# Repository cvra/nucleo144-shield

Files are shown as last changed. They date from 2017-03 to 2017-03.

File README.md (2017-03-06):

# CVRA Nucleo144 shield

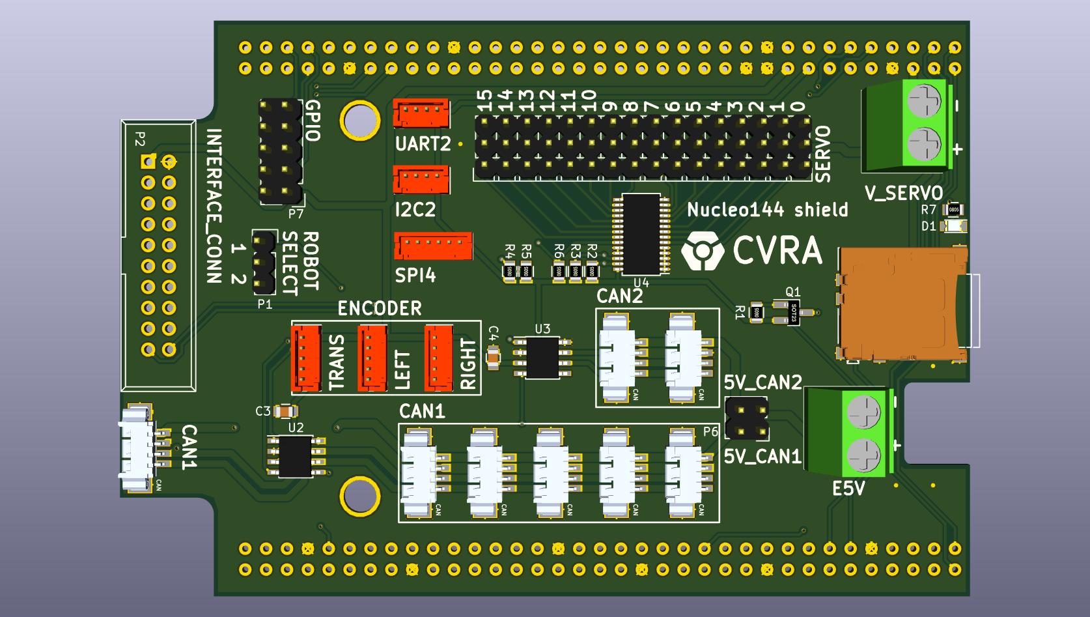
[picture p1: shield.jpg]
assembled PCB


## Requirements list
* Alim en entrée
 - 5V, bus + nucleo + shield (borne à visser)
 - 6V, servo (borne à visser)
* debug connector
* 2x CAN interface with CAN transceiver:
  - 6x Connector for one CAN interface (mounted as needed)
  - 3x Connector for other CAN interface (mounted as needed)
* Interface panel connector (20 pin)
  - 5V, GND (2 pin)
  - 2x CAN for debug (1 for each interface) (4 pin)
  - RGB LED (3 GPIO to control) (3 pin)
  - I/O (11 pin)
* 15x RC-Servo output: connecteur 3pin 2.54mm standard (+,-,signal). use PWM if available and GPIO for the rest (software PWM)
* 2x Encoder connector (5-pin Molex CHA, CHB, CHN, 5V, GND)
(3x Encoder connector if I/O available on MCU)
* Additional connectors (if I/O available on MCU)
  - 1x I2C Molex
  - 1x UART Molex
  - 1x SPI Molex
  - 4x GPIO (with 4x GND) on 2.54mm standard pin holes (no connector)
  - 1x 5V power to power board and distribute over CAN
* SDCard/SPI-flash for logging
* Mechanical dimension
  - Width and length, max same as Nucleo-144 board (70mmx108mm)
  - Maximum mechanical available space including output cable for Nucleo board and shield ( height = 36mm, lenght = 136.5mm)

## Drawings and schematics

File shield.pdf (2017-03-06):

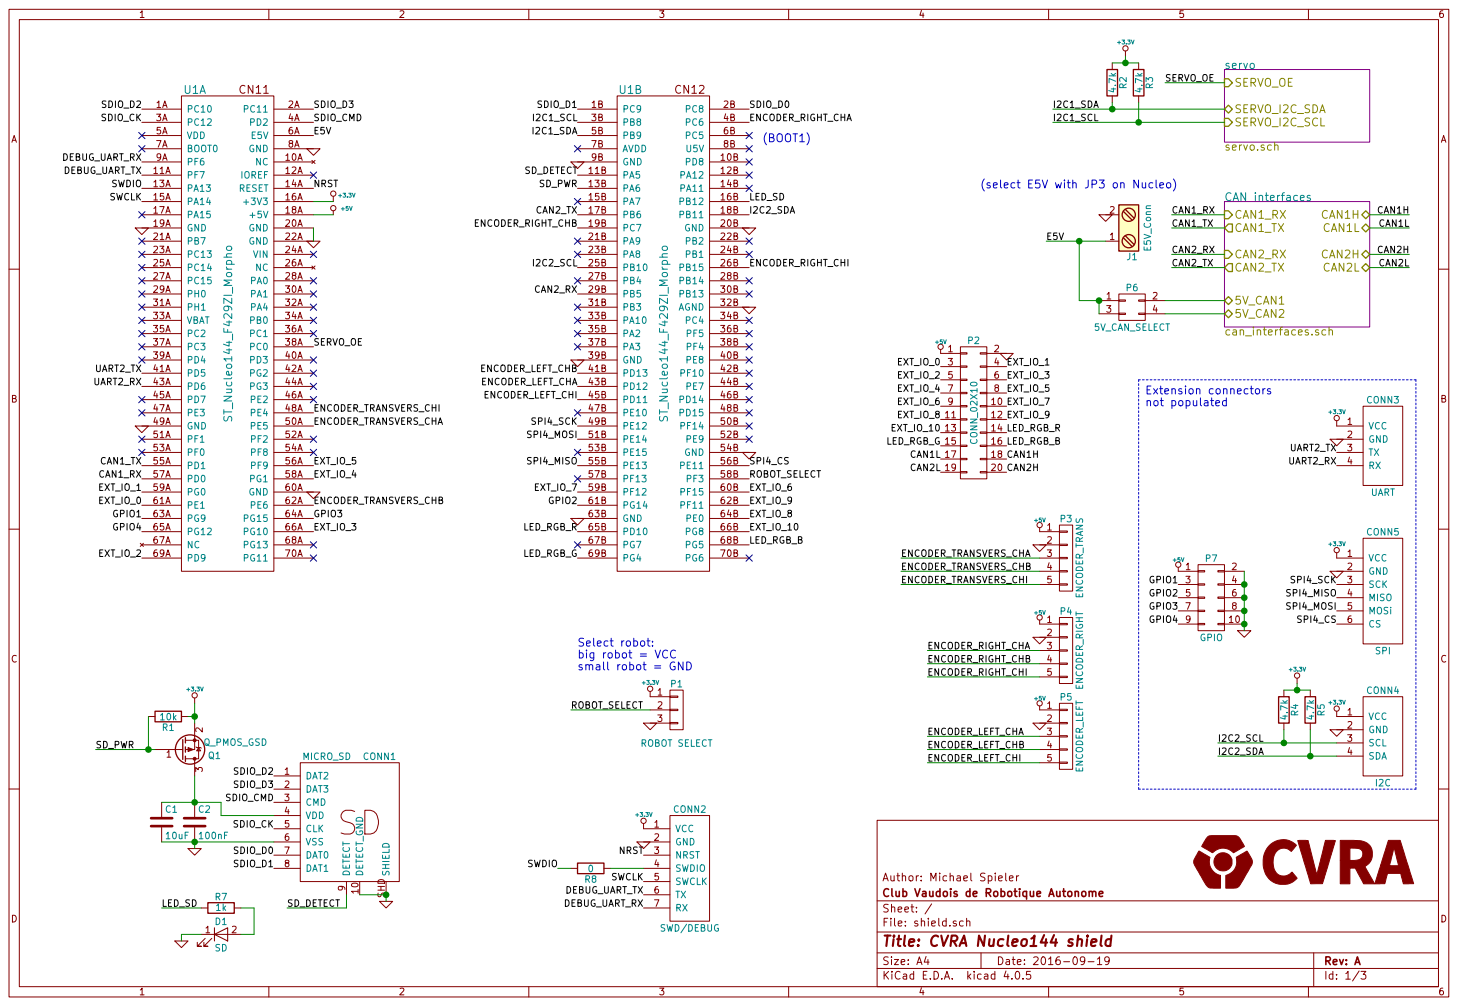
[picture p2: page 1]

Author: Michael Spieler
File: shield.sch Sheet: / Club Vaudois de Robotique Autonome

Id: 1/3 Title: CVRA Nucleo144 shield

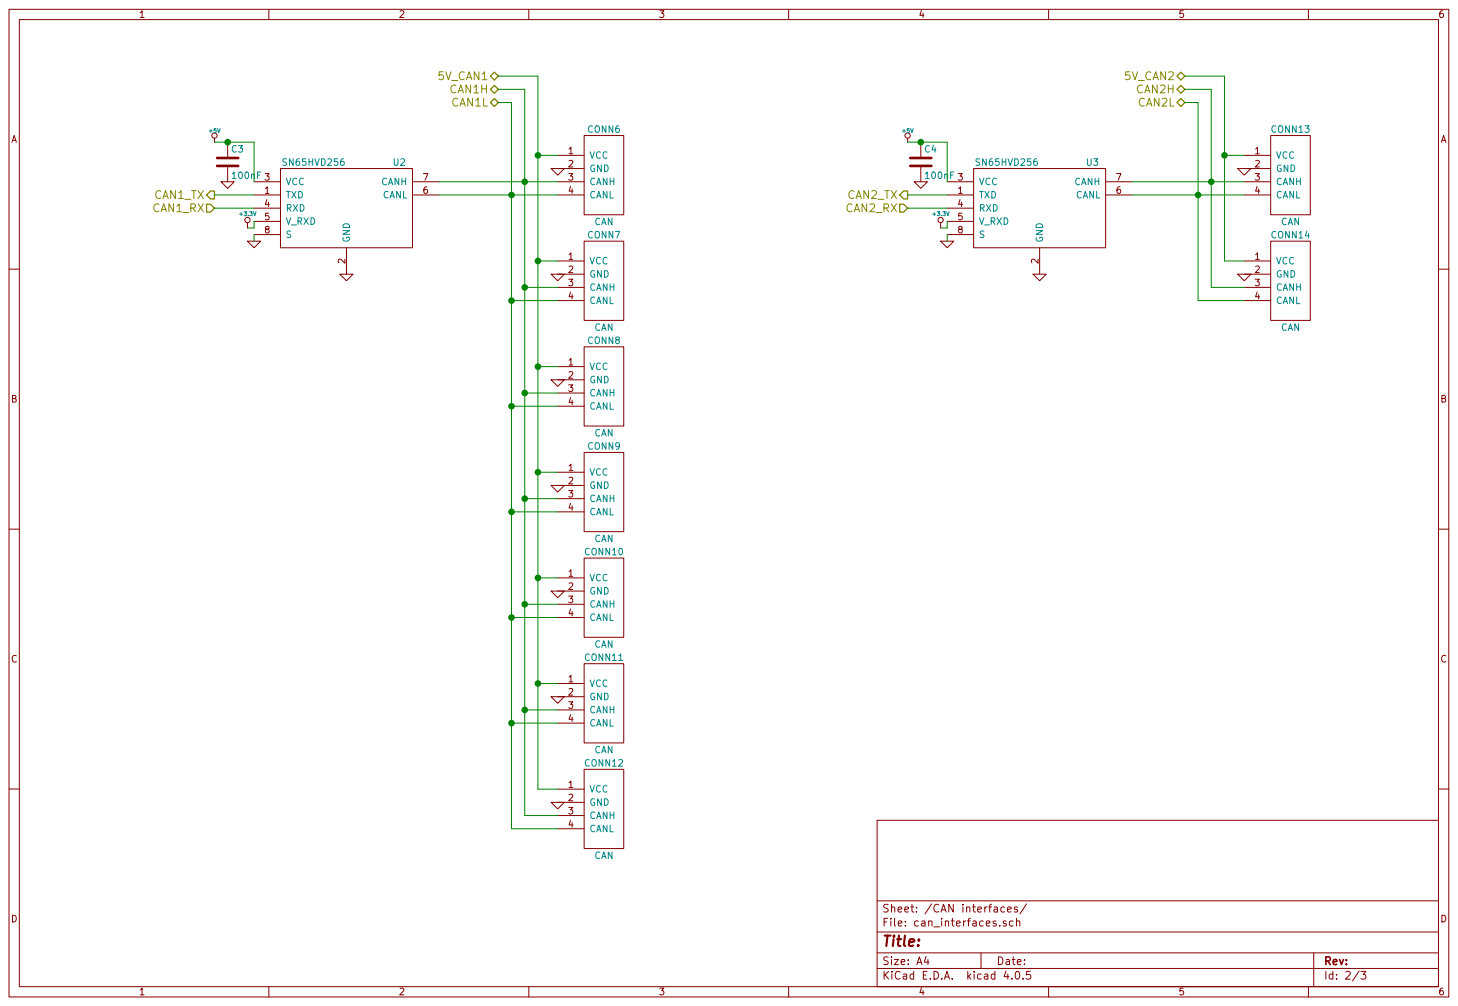
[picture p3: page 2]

File: can_interfaces.sch Sheet: /CAN interfaces/

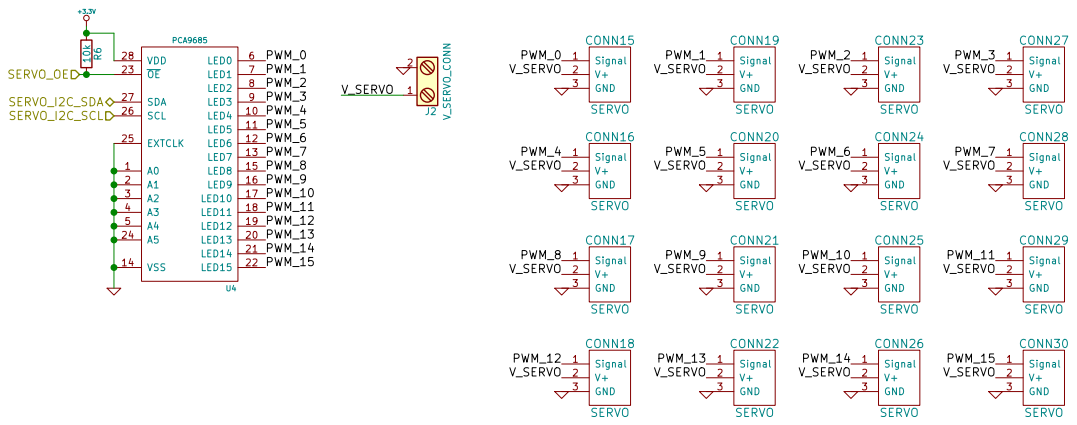
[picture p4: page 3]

Id: 3/3 Title: File: servo.sch Sheet: /servo/

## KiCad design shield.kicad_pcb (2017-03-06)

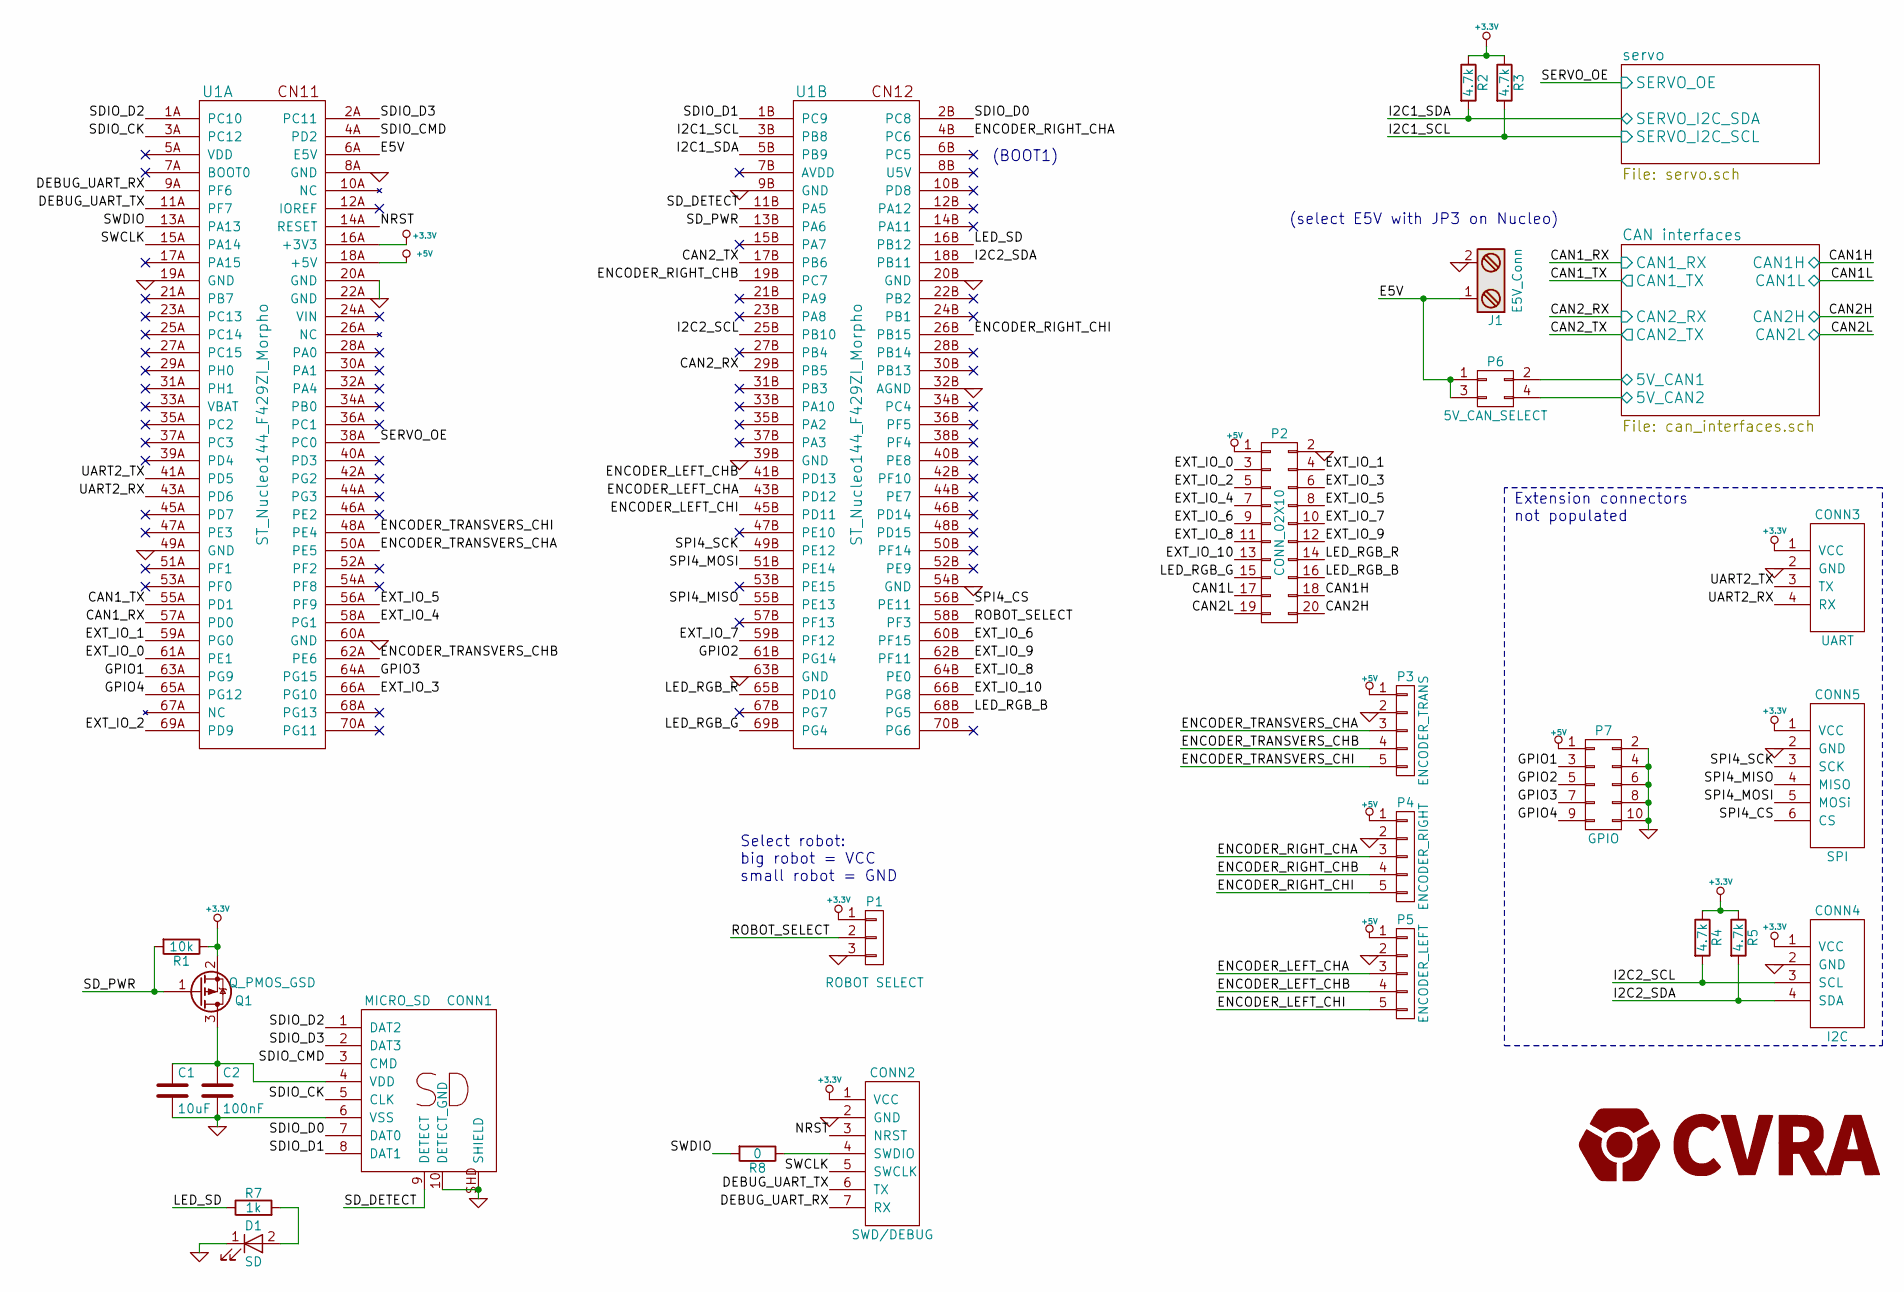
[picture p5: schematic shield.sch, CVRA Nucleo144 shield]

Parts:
C1: 10uF; C_0805
C2: 100nF; C_0805
CONN1: MICRO_SD; _Molex-microSD-502570-0893
CONN2: SWD/DEBUG; Molex_PicoBlade_53261-0771_07x1.25mm_Angled
CONN3: UART; Molex-PicoBlade-4
CONN4: I2C; Molex-PicoBlade-4
CONN5: SPI; Molex-PicoBlade-6
D1: SD; LED_0805
J1: E5V_Conn; TerminalBlock_Pheonix_MKDS1.5-2pol
P1: ROBOT SELECT; Pin_Header_Straight_1x03
P2: CONN_02X10; IDC_Header_Straight_20pins
P3: ENCODER_TRANS; Molex-PicoBlade-5
P4: ENCODER_RIGHT; Molex-PicoBlade-5
P5: ENCODER_LEFT; Molex-PicoBlade-5
P6: 5V_CAN_SELECT; Pin_Header_Straight_2x02
P7: GPIO; Pin_Header_Straight_2x05
Q1: Q_PMOS_GSD; SOT-23_Handsoldering
R1: 10k; R_0805
R2, R3, R4, R5: 4.7k; R_0805
R7: 1k; R_0805
R8: 0; R_0805
U1: ST_Nucleo144_F429ZI_Morpho

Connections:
+3.3V: CONN2.1 (VCC), CONN3.1 (VCC), CONN4.1 (VCC), CONN5.1 (VCC), P1.1, Q1.2 (S), R1.1, R2.1, R3.1, R4.1, R5.1, U1.16A (+3V3); also elsewhere on the board
+5V: P2.1, P3.1, P4.1, P5.1, P7.1, U1.18A (+5V); also elsewhere on the board
/CAN1H: P2.18; also elsewhere on the board
/CAN1L: P2.17; also elsewhere on the board
/CAN1_RX: U1.57A (PD0); also elsewhere on the board
/CAN1_TX: U1.55A (PD1); also elsewhere on the board
/CAN2H: P2.20; also elsewhere on the board
/CAN2L: P2.19; also elsewhere on the board
/CAN2_RX: U1.29B (PB5); also elsewhere on the board
/CAN2_TX: U1.17B (PB6); also elsewhere on the board
/CAN interfaces/5V_CAN1: P6.2; also elsewhere on the board
/CAN interfaces/5V_CAN2: P6.4; also elsewhere on the board
/DEBUG_UART_RX: CONN2.7 (RX), U1.9A (PF6)
/DEBUG_UART_TX: CONN2.6 (TX), U1.11A (PF7)
/E5V: J1.1, P6.1, P6.3, U1.6A (E5V)
/ENCODER_LEFT_CHA: P5.3, U1.43B (PD12)
/ENCODER_LEFT_CHB: P5.4, U1.41B (PD13)
/ENCODER_LEFT_CHI: P5.5, U1.45B (PD11)
/ENCODER_RIGHT_CHA: P4.3, U1.4B (PC6)
/ENCODER_RIGHT_CHB: P4.4, U1.19B (PC7)
/ENCODER_RIGHT_CHI: P4.5, U1.26B (PB15)
/ENCODER_TRANSVERS_CHA: P3.3, U1.50A (PE5)
/ENCODER_TRANSVERS_CHB: P3.4, U1.62A (PE6)
/ENCODER_TRANSVERS_CHI: P3.5, U1.48A (PE4)
/EXT_IO_0: P2.3, U1.61A (PE1)
/EXT_IO_1: P2.4, U1.59A (PG0)
/EXT_IO_2: P2.5, U1.69A (PD9)
/EXT_IO_3: P2.6, U1.66A (PG10)
/EXT_IO_4: P2.7, U1.58A (PG1)
/EXT_IO_5: P2.8, U1.56A (PF9)
/EXT_IO_6: P2.9, U1.60B (PF15)
/EXT_IO_7: P2.10, U1.59B (PF12)
/EXT_IO_8: P2.11, U1.64B (PE0)
/EXT_IO_9: P2.12, U1.62B (PF11)
/EXT_IO_10: P2.13, U1.66B (PG8)
/GPIO1: P7.3, U1.63A (PG9)
/GPIO2: P7.5, U1.61B (PG14)
/GPIO3: P7.7, U1.64A (PG15)
/GPIO4: P7.9, U1.65A (PG12)
/I2C1_SCL: R3.2, U1.3B (PB8); also elsewhere on the board
/I2C1_SDA: R2.2, U1.5B (PB9); also elsewhere on the board
/I2C2_SCL: CONN4.3 (SCL), R4.2, U1.25B (PB10)
/I2C2_SDA: CONN4.4 (SDA), R5.2, U1.18B (PB11)
/LED_RGB_B: P2.16, U1.68B (PG5)
/LED_RGB_G: P2.15, U1.69B (PG4)
/LED_RGB_R: P2.14, U1.65B (PD10)
/LED_SD: R7.1, U1.16B (PB12)
/NRST: CONN2.3 (NRST), U1.14A (RESET)
/ROBOT_SELECT: P1.2, U1.58B (PF3)
/SDIO_CK: CONN1.5 (CLK), U1.3A (PC12)
/SDIO_CMD: CONN1.3 (CMD), U1.4A (PD2)
/SDIO_D0: CONN1.7 (DAT0), U1.2B (PC8)
/SDIO_D1: CONN1.8 (DAT1), U1.1B (PC9)
/SDIO_D2: CONN1.1 (DAT2), U1.1A (PC10)
/SDIO_D3: CONN1.2 (DAT3), U1.2A (PC11)
/SD_DETECT: CONN1.9 (DETECT), U1.11B (PA5)
/SD_PWR: Q1.1 (G), R1.2, U1.13B (PA6)
/SERVO_OE: U1.38A (PC0); also elsewhere on the board
/SPI4_CS: CONN5.6 (CS), U1.56B (PE11)
/SPI4_MISO: CONN5.4 (MISO), U1.55B (PE13)
/SPI4_MOSI: CONN5.5 (MOSi), U1.51B (PE14)
/SPI4_SCK: CONN5.3 (SCK), U1.49B (PE12)
/SWCLK: CONN2.5 (SWCLK), U1.15A (PA14)
/SWDIO: R8.2, U1.13A (PA13)
/UART2_RX: CONN3.4 (RX), U1.43A (PD6)
/UART2_TX: CONN3.3 (TX), U1.41A (PD5)
GND: C1.2, C2.2, CONN1.6 (VSS), CONN1.10 (DETECT_GND), CONN1.SHD (SHIELD), CONN2.2 (GND), CONN3.2 (GND), CONN4.2 (GND), CONN5.2 (GND), D1.1 (K), J1.2, P1.3, P2.2, P3.2, P4.2, P5.2, P7.2, P7.4, P7.6, P7.8, P7.10, U1.8A (GND), U1.9B (GND), U1.19A (GND), U1.20A (GND), U1.20B (GND), U1.22A (GND), U1.32B (AGND), U1.39B (GND), U1.49A (GND), U1.54B (GND), U1.60A (GND), U1.63B (GND); also elsewhere on the board
unnamed: C1.1, C2.1, CONN1.4 (VDD), Q1.3 (D)
unnamed: CONN2.4 (SWDIO), R8.1
unnamed: D1.2 (A), R7.2

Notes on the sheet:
Select robot: big robot = VCC small robot = GND
(BOOT1)
(select E5V with JP3 on Nucleo)
Extension connectors not populated

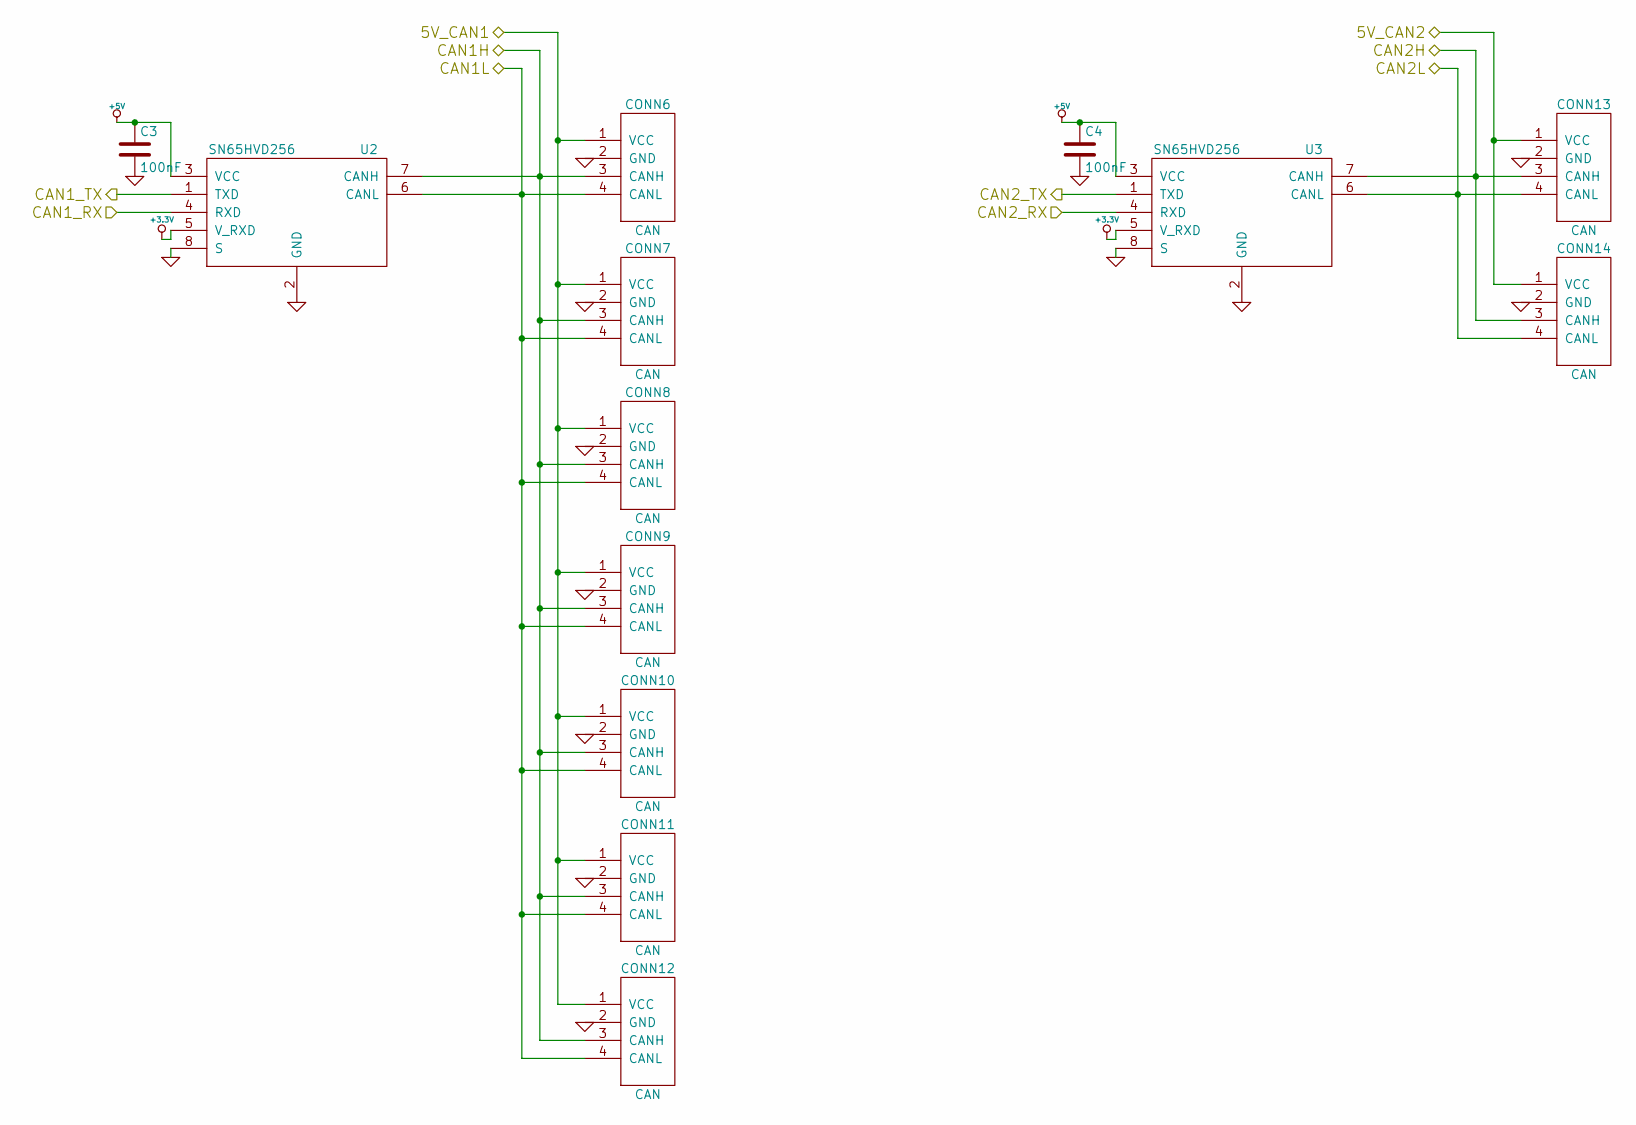
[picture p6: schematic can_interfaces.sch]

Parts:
C3, C4: 100nF; C_0805
CONN6, CONN7, CONN8, CONN9, CONN10, CONN11, CONN12, CONN13, CONN14: CAN; _Molex-PicoBlade-SMD-4
U2, U3: SN65HVD256; SOIC-8_3.9x4.9mm_Pitch1.27mm

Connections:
+3.3V: U2.5 (V_RXD), U3.5 (V_RXD); also elsewhere on the board
+5V: C3.1, C4.1, U2.3 (VCC), U3.3 (VCC); also elsewhere on the board
/CAN1H: CONN6.3 (CANH), CONN7.3 (CANH), CONN8.3 (CANH), CONN9.3 (CANH), CONN10.3 (CANH), CONN11.3 (CANH), CONN12.3 (CANH), U2.7 (CANH); also elsewhere on the board
/CAN1L: CONN6.4 (CANL), CONN7.4 (CANL), CONN8.4 (CANL), CONN9.4 (CANL), CONN10.4 (CANL), CONN11.4 (CANL), CONN12.4 (CANL), U2.6 (CANL); also elsewhere on the board
/CAN1_RX: U2.4 (RXD); also elsewhere on the board
/CAN1_TX: U2.1 (TXD); also elsewhere on the board
/CAN2H: CONN13.3 (CANH), CONN14.3 (CANH), U3.7 (CANH); also elsewhere on the board
/CAN2L: CONN13.4 (CANL), CONN14.4 (CANL), U3.6 (CANL); also elsewhere on the board
/CAN2_RX: U3.4 (RXD); also elsewhere on the board
/CAN2_TX: U3.1 (TXD); also elsewhere on the board
/CAN interfaces/5V_CAN1: CONN6.1 (VCC), CONN7.1 (VCC), CONN8.1 (VCC), CONN9.1 (VCC), CONN10.1 (VCC), CONN11.1 (VCC), CONN12.1 (VCC); also elsewhere on the board
/CAN interfaces/5V_CAN2: CONN13.1 (VCC), CONN14.1 (VCC); also elsewhere on the board
GND: C3.2, C4.2, CONN6.2 (GND), CONN6.MECH (GND), CONN7.2 (GND), CONN7.MECH (GND), CONN8.2 (GND), CONN8.MECH (GND), CONN9.2 (GND), CONN9.MECH (GND), CONN10.2 (GND), CONN10.MECH (GND), CONN11.2 (GND), CONN11.MECH (GND), CONN12.2 (GND), CONN12.MECH (GND), CONN13.2 (GND), CONN13.MECH (GND), CONN14.2 (GND), CONN14.MECH (GND), U2.2 (GND), U2.8 (S), U3.2 (GND), U3.8 (S); also elsewhere on the board

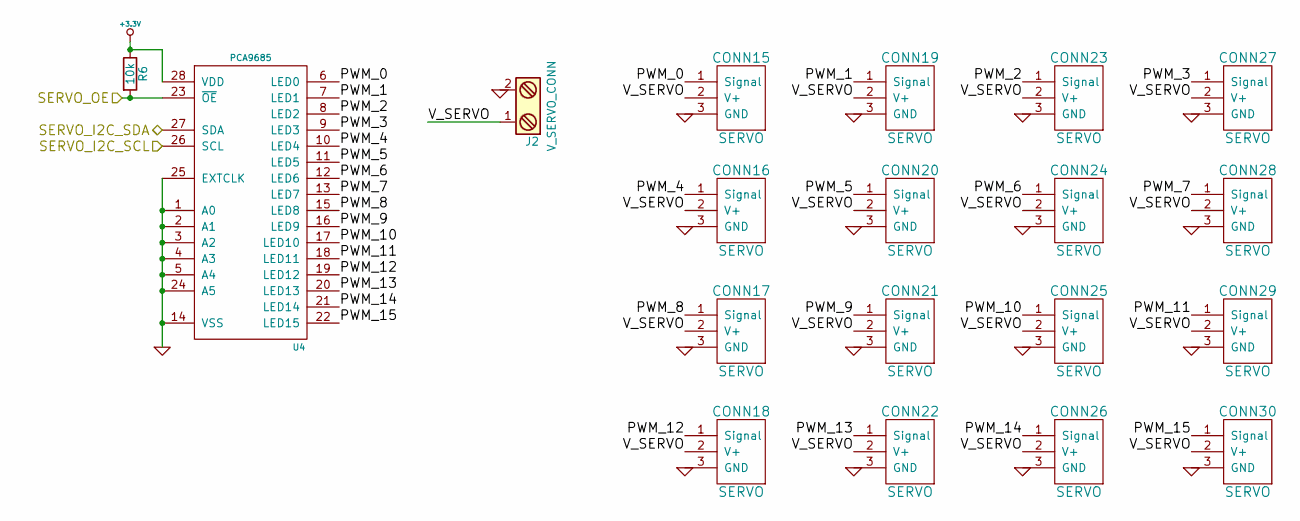
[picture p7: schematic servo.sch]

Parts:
CONN15, CONN16, CONN17, CONN18, CONN19, CONN20, CONN21, CONN22, CONN23, CONN24, CONN25, CONN26, CONN27, CONN28, CONN29, CONN30: SERVO; Pin_Header_Straight_1x03
J2: V_SERVO_CONN; TerminalBlock_Pheonix_MKDS1.5-2pol
R6: 10k; R_0805
U4: PCA9685; TSSOP-28_4.4x9.7mm_Pitch0.65mm

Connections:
+3.3V: R6.1, U4.28 (VDD); also elsewhere on the board
/I2C1_SCL: U4.26 (SCL); also elsewhere on the board
/I2C1_SDA: U4.27 (SDA); also elsewhere on the board
/SERVO_OE: R6.2, U4.23 (~OE); also elsewhere on the board
/servo/PWM_0: CONN15.1 (Signal), U4.6 (LED0)
/servo/PWM_1: CONN19.1 (Signal), U4.7 (LED1)
/servo/PWM_2: CONN23.1 (Signal), U4.8 (LED2)
/servo/PWM_3: CONN27.1 (Signal), U4.9 (LED3)
/servo/PWM_4: CONN16.1 (Signal), U4.10 (LED4)
/servo/PWM_5: CONN20.1 (Signal), U4.11 (LED5)
/servo/PWM_6: CONN24.1 (Signal), U4.12 (LED6)
/servo/PWM_7: CONN28.1 (Signal), U4.13 (LED7)
/servo/PWM_8: CONN17.1 (Signal), U4.15 (LED8)
/servo/PWM_9: CONN21.1 (Signal), U4.16 (LED9)
/servo/PWM_10: CONN25.1 (Signal), U4.17 (LED10)
/servo/PWM_11: CONN29.1 (Signal), U4.18 (LED11)
/servo/PWM_12: CONN18.1 (Signal), U4.19 (LED12)
/servo/PWM_13: CONN22.1 (Signal), U4.20 (LED13)
/servo/PWM_14: CONN26.1 (Signal), U4.21 (LED14)
/servo/PWM_15: CONN30.1 (Signal), U4.22 (LED15)
/servo/V_SERVO: CONN15.2 (V+), CONN16.2 (V+), CONN17.2 (V+), CONN18.2 (V+), CONN19.2 (V+), CONN20.2 (V+), CONN21.2 (V+), CONN22.2 (V+), CONN23.2 (V+), CONN24.2 (V+), CONN25.2 (V+), CONN26.2 (V+), CONN27.2 (V+), CONN28.2 (V+), CONN29.2 (V+), CONN30.2 (V+), J2.1
GND: CONN15.3 (GND), CONN16.3 (GND), CONN17.3 (GND), CONN18.3 (GND), CONN19.3 (GND), CONN20.3 (GND), CONN21.3 (GND), CONN22.3 (GND), CONN23.3 (GND), CONN24.3 (GND), CONN25.3 (GND), CONN26.3 (GND), CONN27.3 (GND), CONN28.3 (GND), CONN29.3 (GND), CONN30.3 (GND), J2.2, U4.1 (A0), U4.2 (A1), U4.3 (A2), U4.4 (A3), U4.5 (A4), U4.14 (VSS), U4.24 (A5), U4.25 (EXTCLK); also elsewhere on the board

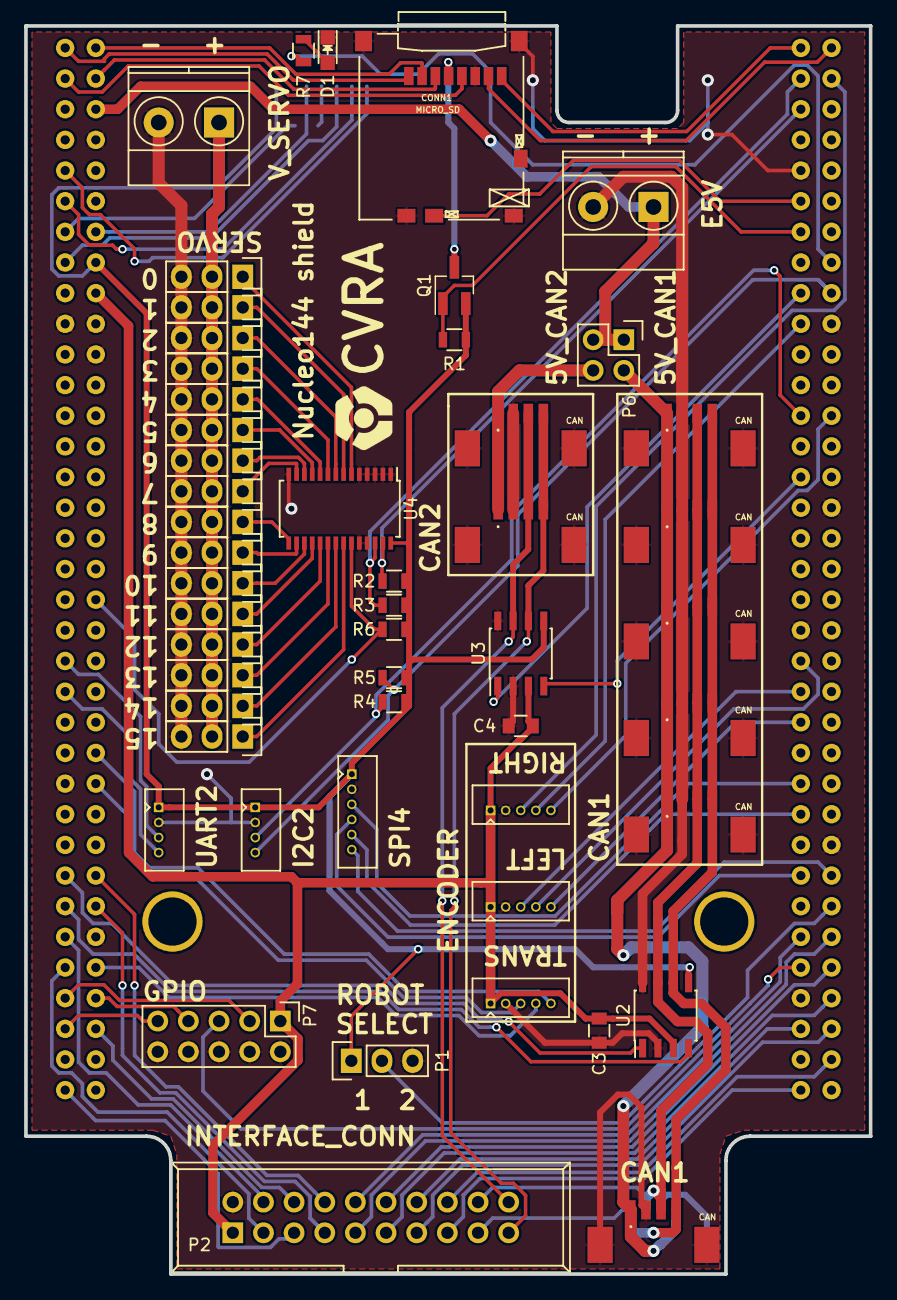
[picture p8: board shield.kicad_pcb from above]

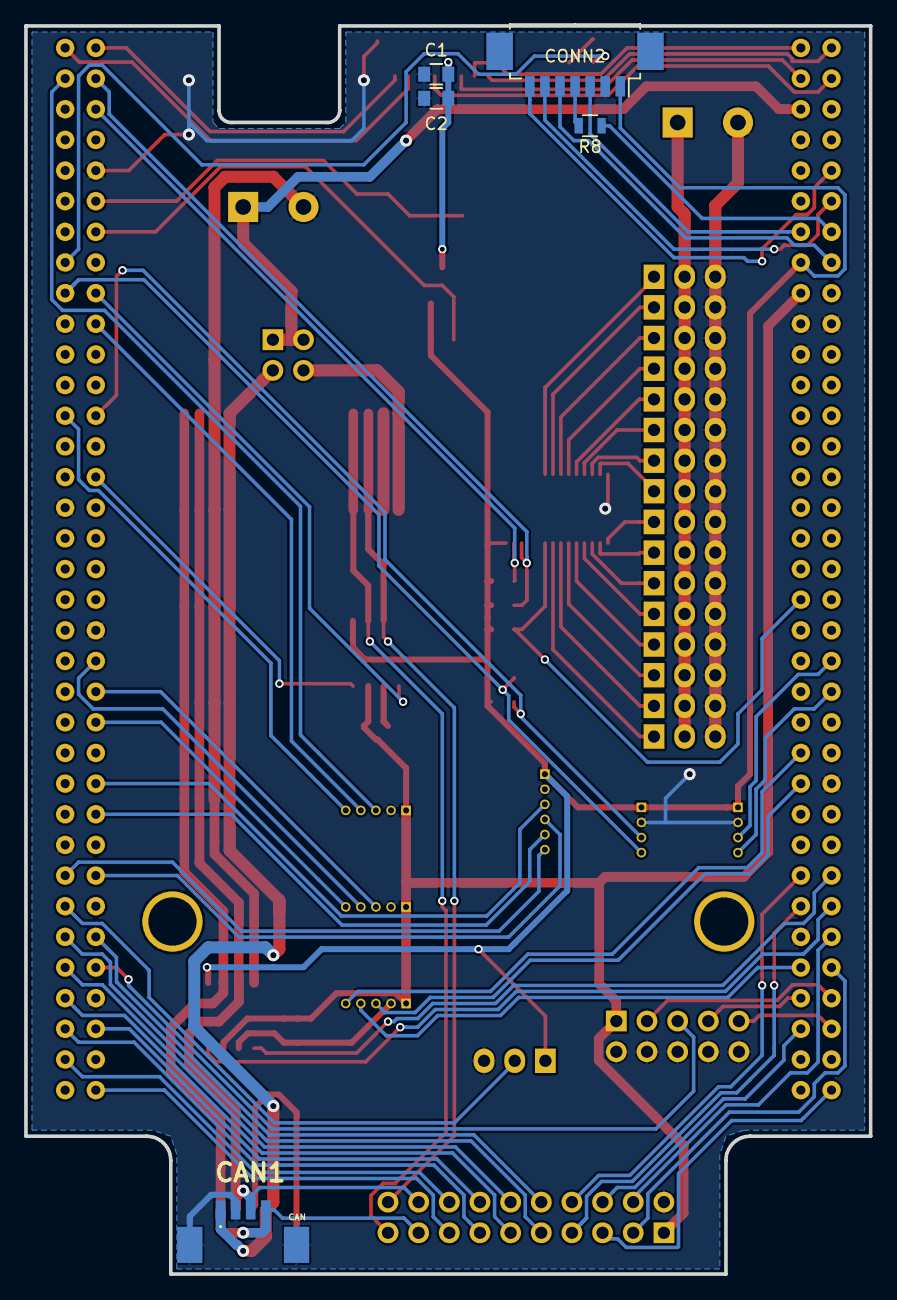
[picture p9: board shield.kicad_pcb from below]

Board: 2 copper layers, 70.0 x 103.4 mm, 59 parts (5 on the bottom side), 87 nets.

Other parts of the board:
_M2, _M2#2: VAL**; _M2

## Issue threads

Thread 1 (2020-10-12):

Any possibility for zio connector support

Robokishan, 2020-10-12:

nuft, 2020-10-12:
Unfortunately, we‘re no longer actively using the Nucleo shield since we switched to a Raspberry Pi.

Closed 2020-10-12.

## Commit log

2016-09-19 start with schematic
    [shield.kicad_pcb, shield.sch]
2016-10-31 add CAN interfaces with connectors
    [can_interfaces.sch, shield.sch]
2016-11-06 SD card
    [shield.sch]
2016-11-21 interface panel connector
    [can_interfaces.sch, shield.sch]
2016-12-21 gpio assignment, servos PWM chip
    [can_interfaces.sch, servo.sch, shield.sch]
2017-01-04 pin assignment, separate CAN_5V
    [can_interfaces.sch, shield.sch]
2017-02-22 pin assignment, symbol placement
    [shield.sch]
2017-03-04 footprint assignment
    [can_interfaces.sch, servo.sch, shield.sch]
2017-03-04 place parts in PCB
    [can_interfaces.sch, servo.sch, shield.kicad_pcb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]
2017-03-06 PCB routing
    [can_interfaces.sch, servo.sch, shield.kicad_pcb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]
2017-03-06 change some GPIOs, finish routing
    [shield.kicad_pcb, shield.sch]
2017-03-06 fix SD PMOS switch pinout
    [shield.kicad_pcb, shield.sch]
2017-03-06 gerber files
    [shield-B.Cu.gbl, shield-B.Mask.gbs, shield-B.SilkS.gbo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]
